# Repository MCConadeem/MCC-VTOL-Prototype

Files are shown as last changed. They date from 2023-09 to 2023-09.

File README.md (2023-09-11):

# MCC_VTOL_PROTOTYPE
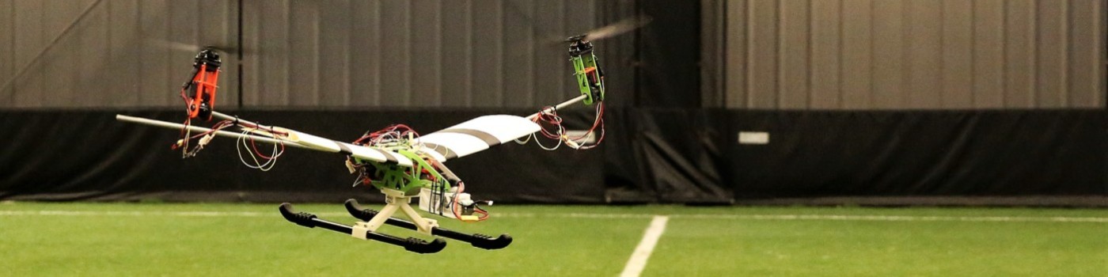
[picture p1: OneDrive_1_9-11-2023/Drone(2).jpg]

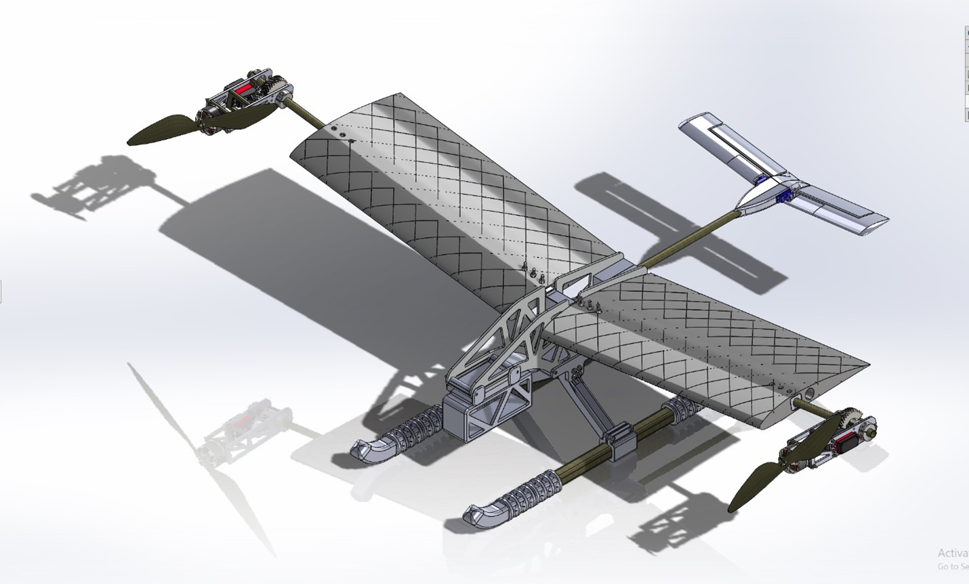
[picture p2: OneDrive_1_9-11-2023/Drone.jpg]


## Introductions

Hello, my name is Omar Nadeem and alongside Pioter Cetner and Maxim Karsav, we are currently undergoing the recreation of one of Tom Stanton's VTOL drones. This is our capstone project for our 2 years at Monroe Community College. For a full in-depth analysis, there will be an engineering notebook for our journey along the way as well as a final report documenting the over-all progress we achieved.

## File Structure
Folders are categorized in sub-assemblies then versions of the full assembly are used with the naming convention of vXXX with the X being replaced with a 0 or the next letter in the alphabet. 
The code for the following aircraft uses an Arduino based Flight Stabilization Package called dRehmflight created by Nicholas Rehm. This is under the dRehmFlight-Master folder. This is well documented and the modifications and our finished journals will be published here at the end of the project.

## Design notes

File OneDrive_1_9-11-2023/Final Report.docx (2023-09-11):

Monroe Community College

Elevation Nation

Maxim Karasev, Piotr Cetner, and Omar Nadeem

May 22nd, 2023

# 1. Executive Summary:

This executive summary provides an overview of our independent project focused on the development of a Vertical Take-Off and Landing (VTOL) Unmanned Aerial Vehicle (UAV). The project aimed to explore the advancements in VTOL technology at a hobbyist level and create a functioning prototype to be upscaled by future students.

Traditional aircraft designs, such as helicopters, planes, and multirotors, have inherent limitations in terms of maneuverability, adaptability, and efficiency. VTOL UAVs combine the vertical take-off and landing capabilities of helicopters and multirotors with the speed and efficiency of fixed-wing aircraft. We decided that a VTOL UAV was an optimal solution to overcome the limitations of traditional aircraft due to its unique combination of capabilities. By utilizing vertical take-off and landing, the VTOL can access confined or hard-to-reach areas, making it suitable for a wide range of applications where a plane simply could not. Furthermore, VTOL aircraft can take off from such an area and then transition to a forward flight mode, allowing it to regain all the traditional advantages a fixed-wing aircraft would have.

Throughout the project, we meticulously analyzed and iteratively improved the design of our VTOL. We encountered and successfully resolved several challenges, such as power distribution issues, control mixing and PID tuning, landing gear and battery mount optimization, and motor and ESC selection. These endeavors involved extensive troubleshooting, redesigning of components, and iterating 3D parts with new revisions. This meticulous approach to design analysis led to significant improvements. Notably, we fine-tuned the PID controls for each axis, ensuring stable and controlled vertical flight. The redesign of the landing gear and battery mount significantly improved rigidity, while the use of LW-HT-PLA material decreased the weight of the craft without sacrificing too much strength.

While we have achieved notable milestones in our project, such as winning the first-place prize in STEM at our college's scholar's day, there are still areas for further development. For example, we are exploring the integration of a DJI FPV camera using the QLiteOSD kit to enhance flight capabilities. The upcoming delivery of new motors will also enable us to continue our testing, expanding it into forward flight.

In conclusion, our independent project has proven to be a valuable exploration of VTOL technology. By combining vertical take-off and landing capabilities with adaptable flight modes, we have created a unique aircraft. By carefully analyzing our design, troubleshooting, and seeking continuous improvement, we have made considerable progress toward our objectives. Our ongoing dedication to the project's advancement ensures that we will continue refining and expanding the capabilities of our VTOL as time passes.

# 2. Table of Contents

Contents

# 3. Design Evolution

Our team embarked on an extensive design process to develop our VTOL. This section highlights the key stages and decisions we made throughout the design stage, providing insights into our design`\ process and the rationale behind our choices. We utilized a combination of CAD modeled parts, circuit schematics, and software code/flowcharts to outline our design journey.

- Initial Ideas and Conceptualization:

The design process began with brainstorming sessions where we explored various concepts and potential solutions. We were motivated by our fascination with VTOL technology and its advantages over traditional aircraft designs. After seeing a VTOL design by Tom Staton, an aerospace engineer, seamlessly transition between vertical take-off and landing and forward flight, we knew we had to build a VTOL ourselves. Initial sketches and concept diagrams captured our early ideas and formed the foundation of our design.

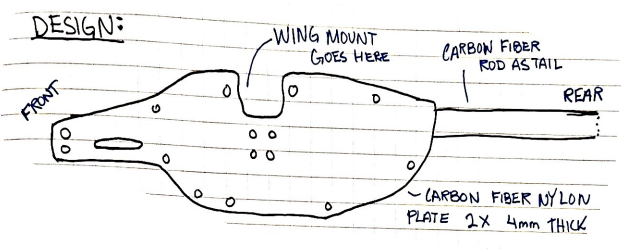
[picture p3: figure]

Figure 1: Initial Sketch

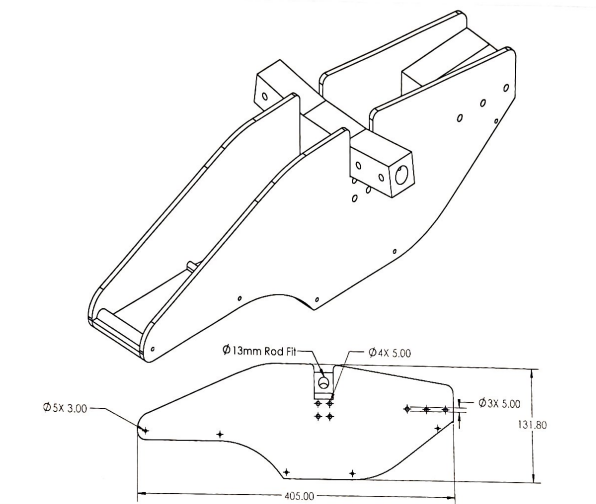
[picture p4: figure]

Figure 2: Initial Assembly

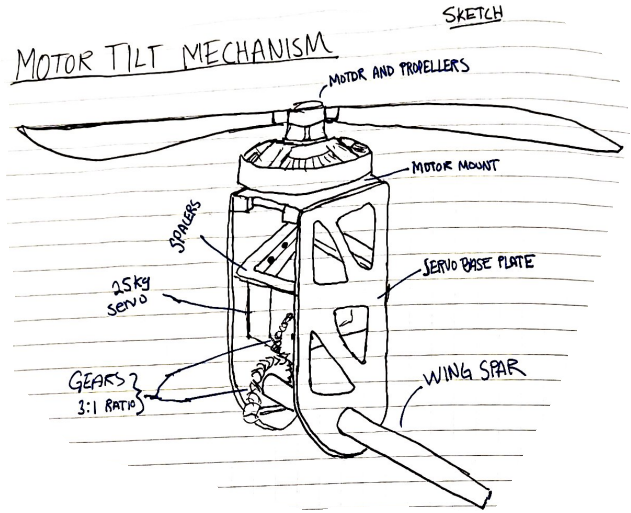
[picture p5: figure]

Figure 3: Motor Tilt Mechanism

- Additive Manufacturing for Rapid Prototyping and Iteration:

Recognizing the potential of 3D printing, we leveraged this technology to fabricate various components of our VTOL. Although we are all mechanical engineering students, and could have manufactured our parts via subtractive manufacturing, we intentionally chose not to do this. The ability to create complex geometries and intricate designs through 3D printing simplifies the design process immensely, as there is near no thought regarding how easy a part is to machine. Additionally, 3d printing reduces the amount of active labor required to prototype so many parts. Traditionally, creating a part for the first time requires someone to be actively working and monitoring any tooling, and this holds true for all future revisions of that part as well. Additive manufacturing allowed us to design a part, press print, go to class, and come back to the finished part in a few hours. If a part ever breaks or needs to be redesigned, then the same process holds true: press print, and come back a few hours later to a finished part. The time savings of additive manufacturing in prototyping is incredible; had we not had access to 3d printers, there is no way we would have been able to proceed at the rate we have been.

- System Architecture and Integration:

Once we had a rough idea of what we wanted to design, we focused on developing a robust system architecture. We identified the critical components, such as the flight controller, motor system, power distribution, and control system, and carefully planned their integration. SolidWorks images and circuit schematics were instrumental in visualizing and refining the system architecture, ensuring proper component placement and interconnectivity.

- Control Mixing and PID Tuning:

Achieving stable flight control was a crucial aspect of our design. We dedicated a considerable amount of time to control mixing and PID tuning, iteratively adjusting the control parameters to maximize performance. None of us had ever had to do any sort of PID tuning, so this was quite a learning experience for us. Software code and flowcharts were used to outline our control algorithms and visualize the flow of information between the inertial measurement unit (IMU) and the flight controller. This process allowed us to refine the control response and ensure stable flight characteristics.

Proportional Integral Derivative

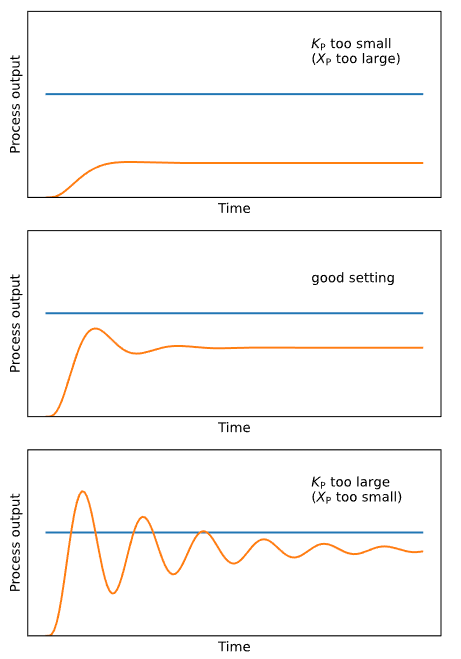
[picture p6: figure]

Figure 4: PID Graphs

1. Proportional Gain (KP): The proportional gain determines the strength of the corrective action applied by the controller. Increasing KP enhances system responsiveness but can introduce overshooting and oscillations, while decreasing KP reduces responsiveness and can result in sluggish behavior. The Proportional Range (XP) limits the range of error values where the proportional action is effective. A wider XP allows proportional control over a larger range, potentially leading to overshooting or instability, while a narrower XP reduces the influence of proportional control and responsiveness near the setpoint.
2. Integration Time (TI): The integration time determines the rate at which the integral action corrects for steady-state errors. Increasing TI strengthens the integral action and reduces steady-state errors, but excessively high values can introduce overshoot and instability.
3. Derivative Time (TD): The derivative time influences the controller's response to the rate of change of the error. Higher TD values introduce more damping, helping to prevent overshooting and oscillations, but extremely high values can introduce response delays and instability.
- Component Optimization and Redesign:

Throughout the design evolution, we encountered challenges and identified areas for improvement. The landing gear and battery mount, for instance, initially relied on zip ties, but we quickly realized the need for a more rigid and secure solution. We iterated on the design, utilizing ABS plastic parts clamped the components onto carbon fiber square rods with M5 bolts. This optimization significantly enhanced the structural integrity of the UAV. We documented these design iterations in our notebooks and captured revised sketches to track the progress.

Figure 5: Landing Gear Redesign

- Material Selection and Testing:

In pursuit of lightweight yet durable components, we explored various materials. Our experimentation led us to LW-HT-PLA, which exhibited superior flexibility and improved impact resistance compared to regular PLA. We tested the material by conducting destructive testing, observing how our wing segments broke when thrown at the ground. These observations allowed us to improve each successive revision of the wings and influenced the final material selection.

Figure 6: Broken Wing

- Future Enhancements:

While our design has reached an advanced stage, we continue to explore opportunities for further development. Integration of a DJI FPV camera using the QLiteOSD kit is one area we are actively working on. Additionally, the impending arrival of new motors will open avenues for testing and refining the forward flight capabilities of our VTOL. Our ongoing commitment to continuous improvement ensures that our design will evolve and adapt as we strive for enhanced performance and functionality.

The design evolution of our VTOL UAV highlights our iterative and detail-oriented approach. Through sketches, SolidWorks images, circuit schematics, and software code/flowcharts, we captured the progression of our design process. From conceptualization to component optimization and material selection, our team's dedication to refinement has shaped the final solution and laid the groundwork for future advancements in VTOL technology.

# 4. UAV Operation

The operational aspects can be attributed to effective PID tuning where it played a crucial role in achieving stable flight by regulating the motor speeds and control surfaces to maintain a balanced and controlled hover. The PID controller monitored the drone's orientation and altitude, adjusting the motor speeds and control surfaces to maintain a stable hover. Through careful tuning of the PID parameters, we were able to achieve a well-balanced hover, where the drone maintained its position and altitude without drifting or exhibiting erratic behavior. After multiple hover tests, we fine-tuned our PID values to create a more stable flight.

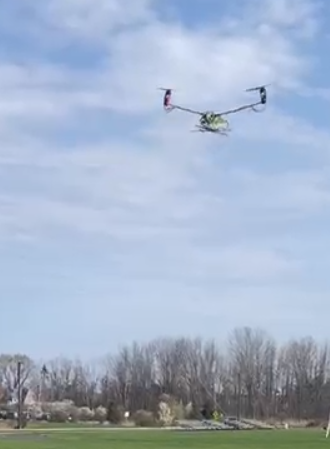
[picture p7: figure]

Figure 7: First Flight

The VTOL prototype demonstrated the ability to hover with only two motors, and this is possible due to the principle of rotational equilibrium and torque balance. When the two motors spin in opposite directions, they create equal and opposite torques, which cancel each other out. This equilibrium allows the drone to hover vertically without any roll or yaw motion.

By carefully adjusting the motor speeds and control surfaces using the PID controller, we were able to maintain this torque balance and achieve a stable hover. The two motors provided the necessary lift to counteract the force of gravity, while the control surfaces helped in adjusting the drone's orientation and stability. It is important to note that achieving a stable hover with only two motors requires precise control and balancing of forces. Any deviation in the motor speeds or control surface inputs can disrupt the torque balance and result in instability or undesired motion. Therefore, the accurate PID tuning and understanding of the physics of vertical flight were essential factors in the success of our hover test.

Overall, the combination of effective PID tuning and a thorough understanding of the physics involved in vertical flight enabled our VTOL prototype to hover successfully, demonstrating its operational capabilities and paving the way for further development and exploration of its flight capabilities.

# 5. Electronics and Software

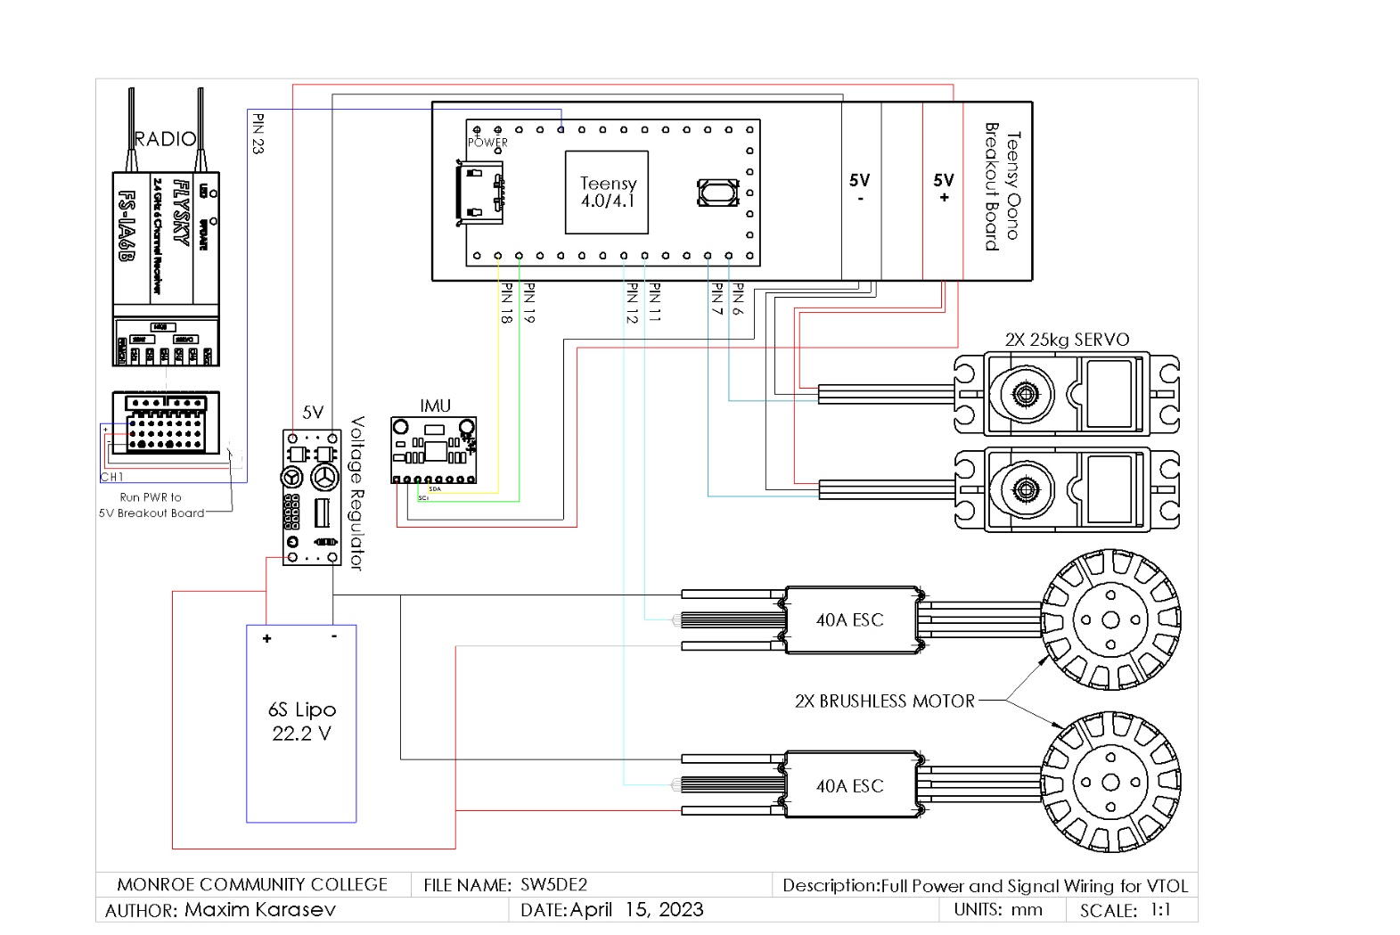
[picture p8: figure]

Figure 8: Circuit Diagram

The electronic circuitry of the project consists of a Teensy 4.0/4.1 microcontroller running the dRehmflight Arduino software developed by Nicholas Rehm. The Teensy serves as the flight controller unit for the project, handling various inputs and outputs.

The Teensy receives signals from two sources: an FS-I6B receiver and an MPU6050 IMU (Inertial Measurement Unit). The FS-I6B receiver is responsible for receiving remote control signals, allowing the user to control the drone. Since we are using PPM (Pulse Position Modulation) as our RX output we only need 1 wire for all 6 channels instead of an individual wire for each channel with SBUS (Serial BUS). The IMU captures motion data from various sensors such as accelerometers, gyroscopes, and magnetometers, providing information about the aircraft's orientation and movement.

The Teensy then processes these input signals and sends commands to several components. The electronic speed controllers (ESCs) receive signals from the Teensy, controlling the motors' speed and direction. This allows the aircraft to achieve controlled movement and adjust its thrust. Additionally, the Teensy sends signals to servos, which are responsible for tilting the motors. By adjusting the servos' positions, the aircraft's pitch and roll can be controlled, enhancing stability and maneuverability.

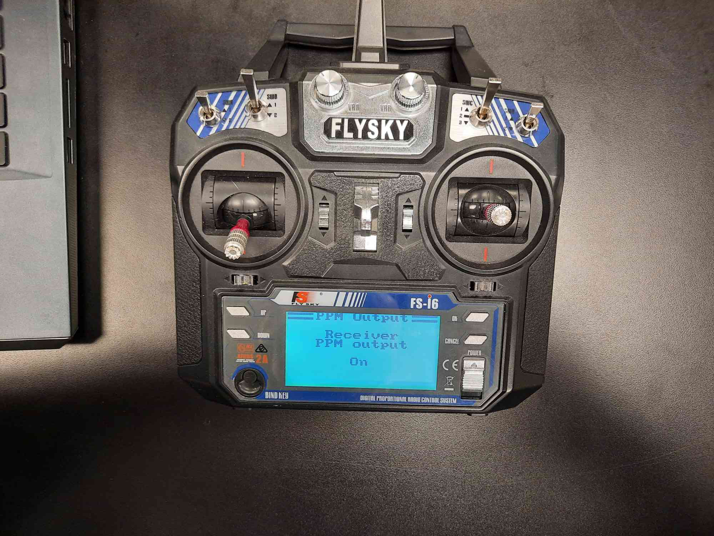
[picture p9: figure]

Figure 9: PPM Output

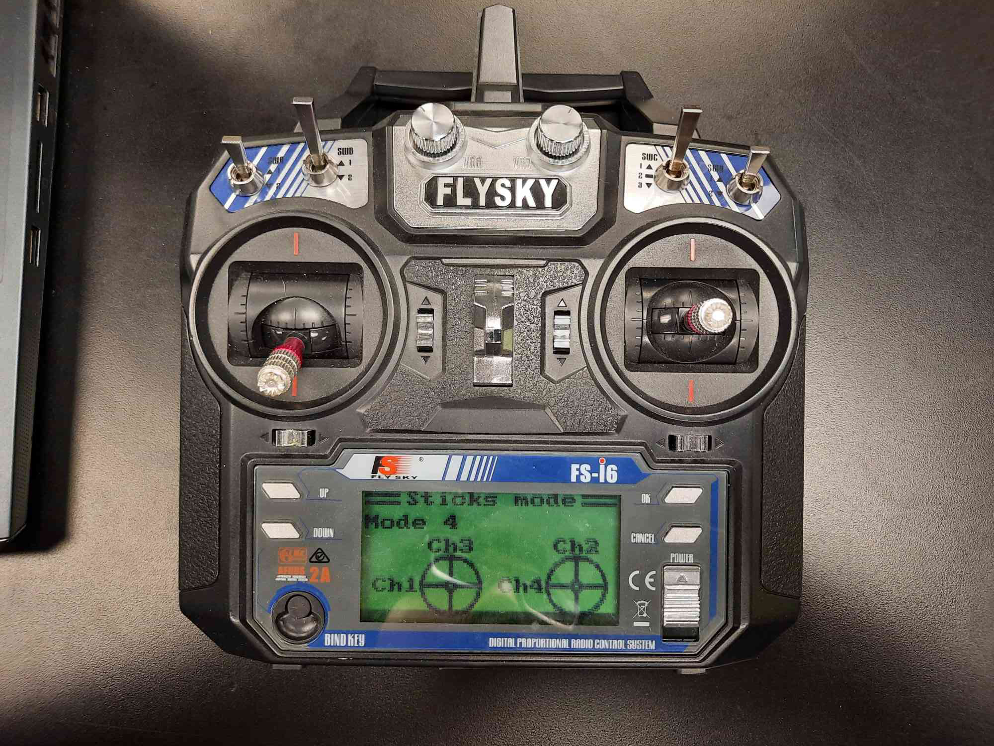
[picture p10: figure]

Figure 10: Sticks Mode

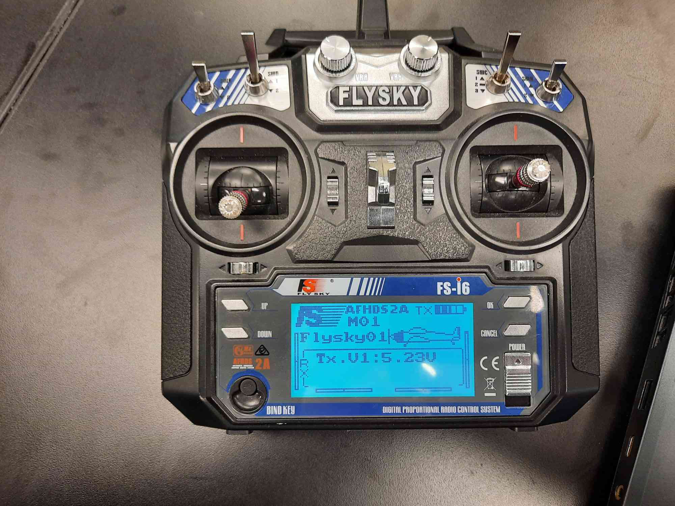
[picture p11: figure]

Figure 11: Trim (Red boxes are where the trim is visually indicated)

The transmitter has multiple settings that are important to note. To simplify the wiring on the drone, we are using PPM on the receiver, so we must make sure the transmitter is outputting the same way. So, on the transmitter PPM output must be activated as seen in figure 9. The next thing is the channels must correspond to what the channels are in the code, so under sticks mode we can change which channels are assigned to which stick. See figure 10. Channels 5 & 6 are auxiliary switches for mode switch and arm. Lastly while flying the drone, you can perform trim which tunes each channel. zero position. This allows you to re-zero the craft’s throttle, roll, pitch, and yaw axis of rotations. These are indicated in the transmitter’s main display as the vertical/horizontal bars which a slider in them. See figure 11.

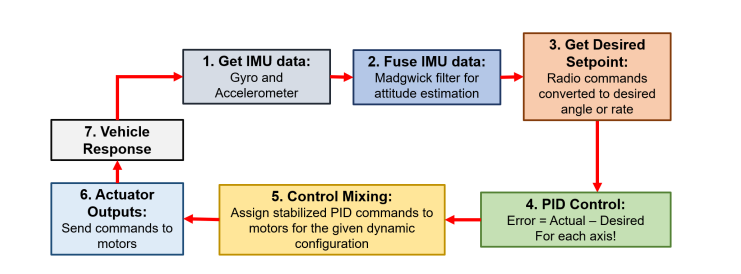
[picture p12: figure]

Figure 12: dRehmFlight control loop (Credit to Nicholas Rehm)

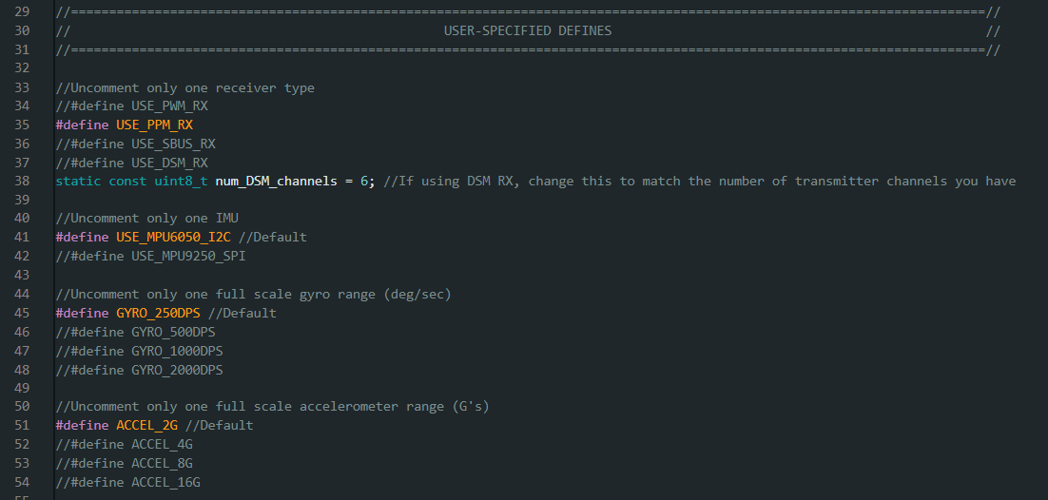
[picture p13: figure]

Figure 13: Hardware Declaration

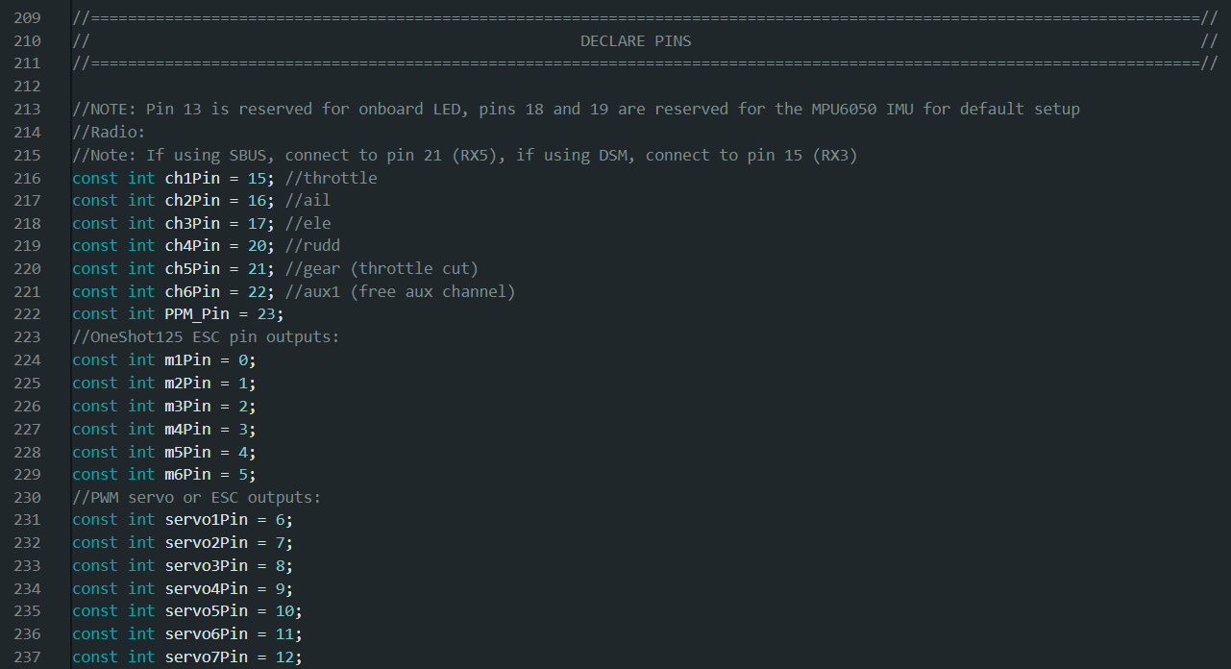
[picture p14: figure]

Figure 14: Pin Declarations

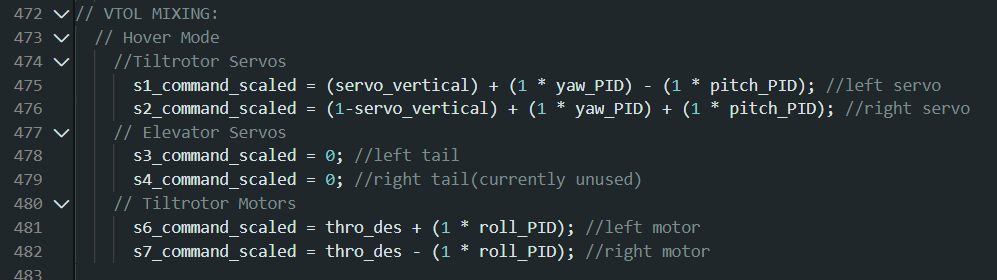
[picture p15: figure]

\

Figure 15: Control Mixing

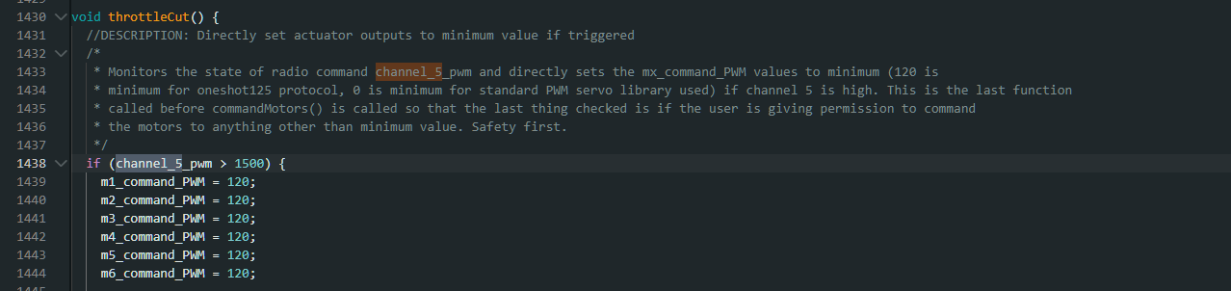
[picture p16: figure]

Figure 16: Throttle Cut Channel Assignment

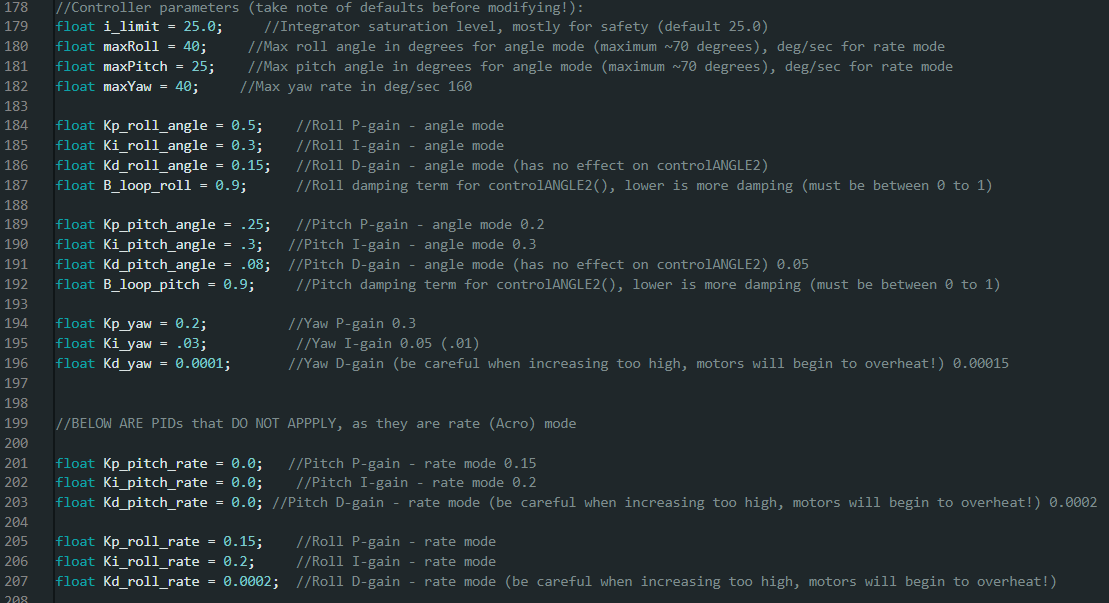
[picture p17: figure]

Figure 17: PID Tuning

The language we are using to code Teensy is Arduino. This language is versatile and has many packages available for almost any use case. A plug-in, Teensyduino created by Paul Stoffregen is used for USB serial connection to the Teensy.

The dRehmflight stabilization package created by Nicholas Rehm provides the framework for creating your own control mixing and tuning for manual flight and auto stabilization. The sections of the code that we edited were the radio, pin declarations, the control mixer function, and the PID values. These were changed in accordance with our specifications for the bi-copter tiltrotor design. The PID values were changed through experimentation. The experimentation involved having the craft held preventing takeoff however had enough degree of freedom to notice if it was drifting in the wrong direction. We did differential thrust (roll) first then yaw and finally pitch tuning in the gym and PAC center here on campus. Currently there is only a hover mode in the code. In the future we will be using Channel 6 switch to have a transition mode that flips between hover and forward flight. Channel 5 is a 2-mode switch which arms the motors giving us the most basic type of failsafe, a kill switch.

# 6. Fabrication Methods

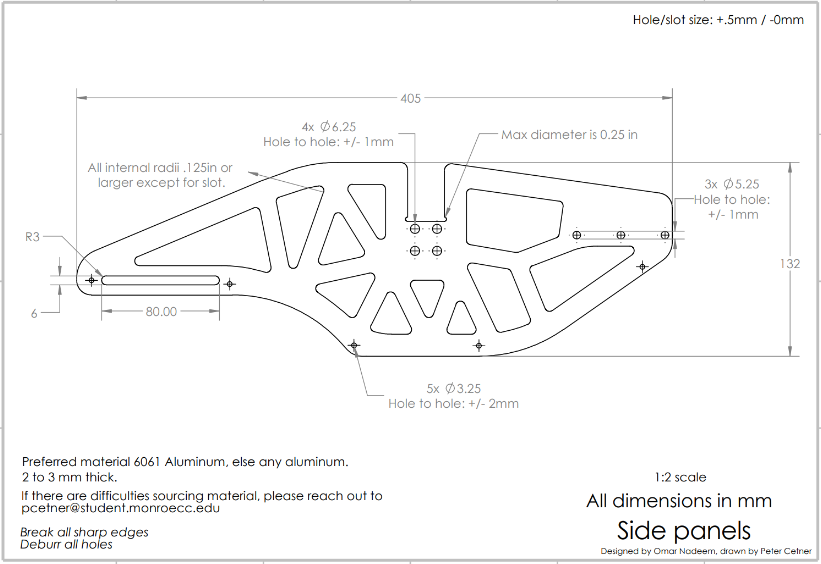
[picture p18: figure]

Figure 18: Side Panel Drawings

Side panels which we 3D printed in PLA because we were not able to get our own machinists to make one in time.

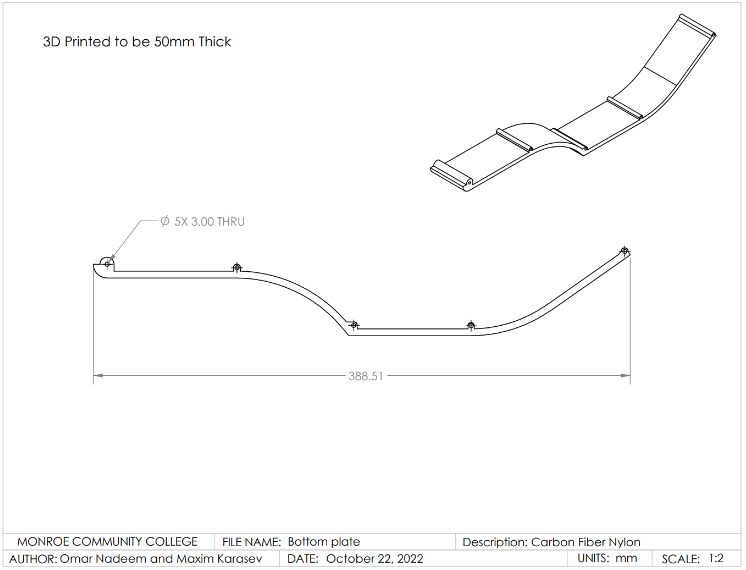
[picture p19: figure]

Figure 19: Bottom plate that attaches side panels.

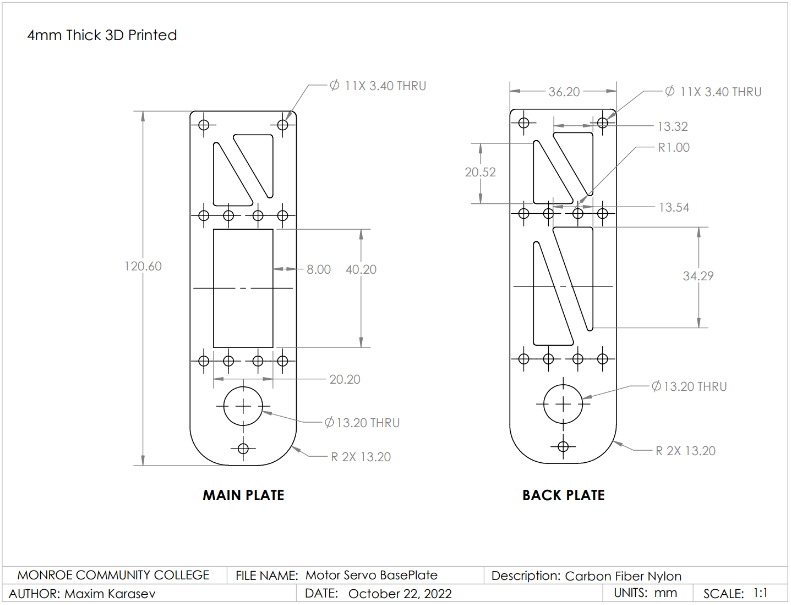
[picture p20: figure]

Figure 20: Base plates for the tilt-mechanism that was originally going to be machined but opted to 3D print in PLA for the prototype.

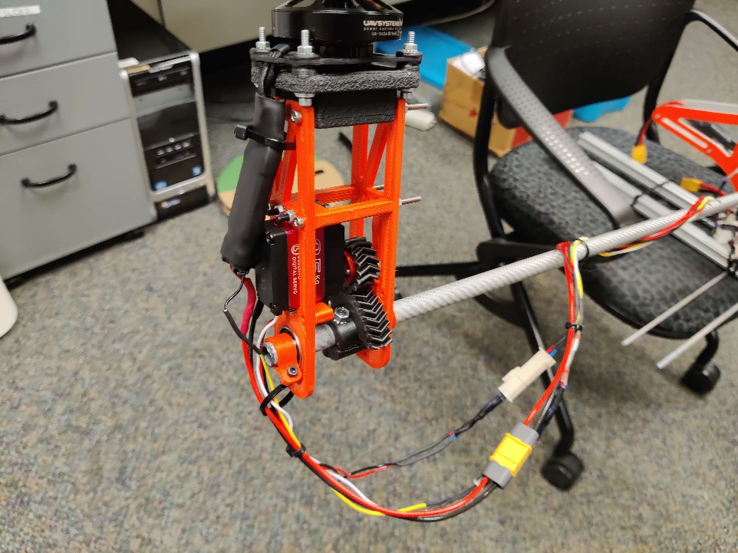
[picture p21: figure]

Figure 21: 3D Tilt-Mechanism Assembly

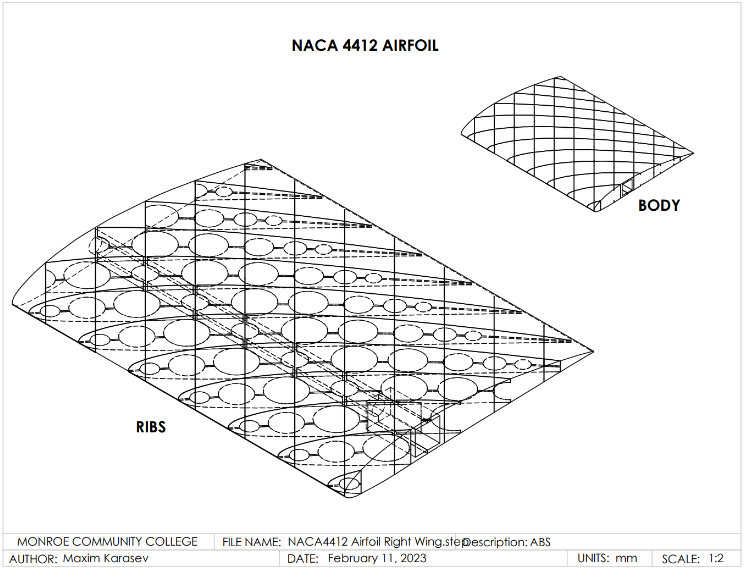
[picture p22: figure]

Figure 22: NACA 4412 Airfoil that was 3D printed in heat resistant light-weight PLA in the final.

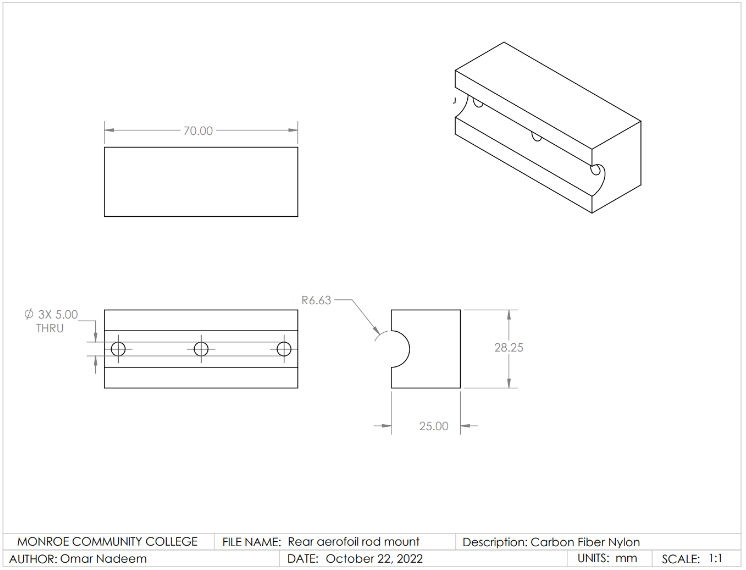
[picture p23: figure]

Figure 23: This attaches to the rear of the side panels to hold the rear carbon fiber rod as tail.

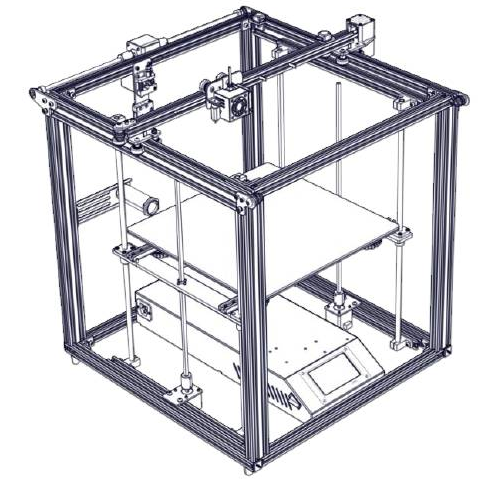
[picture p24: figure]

Ender 5 Plus 3D Printer Method X 3D Printer

Figure 24: 3d Printers

We used the Ender 5 Plus to 3D print parts in PLA or lightweight PLA. Most of our designed parts were fabricated through PLA. We used the Method X for any part that needs to be printed in a stronger material which was Carbon Fiber Nylon. This allowed for any parts that have a lot of forces at play to be stable and reduce the chances of failure.

# 7. Design Analysis:

The design for the tiltrotors provides a reliable and stable way of controlling the thrust vectors of our motors. This allows us to perform stable flight and maintain hover through the stabilization code. Our first test flight was successful in getting off the ground but some more tuning was required as it was unstable in some axis’s. Due to the wind, we couldn’t properly adjust our transmitter trim so after the first flight we headed inside to the PAC center, an indoor field, to tune it further. This proved very useful as it allowed us to further finetune the PID values. This led to the drone being able to take off and the stabilization code kept it in place hovering.

From this stage we redesigned our landing gears as seen in figure 5, moved the battery to the nose and added wings to our carbon fiber rods. This was all done in preparation for the forward flight transition test. With all these redesigns we will need to redo our PID & trim tuning for the hover mode. The forward flight capabilities of this drone are still in progress as we design and prototype the tail section for pitch control in the forward flight. We will also have to add in the forward flight and 2-mode transition switch.

https://youtu.be/snkThKrBGW0

Figure 25: First Flight Video

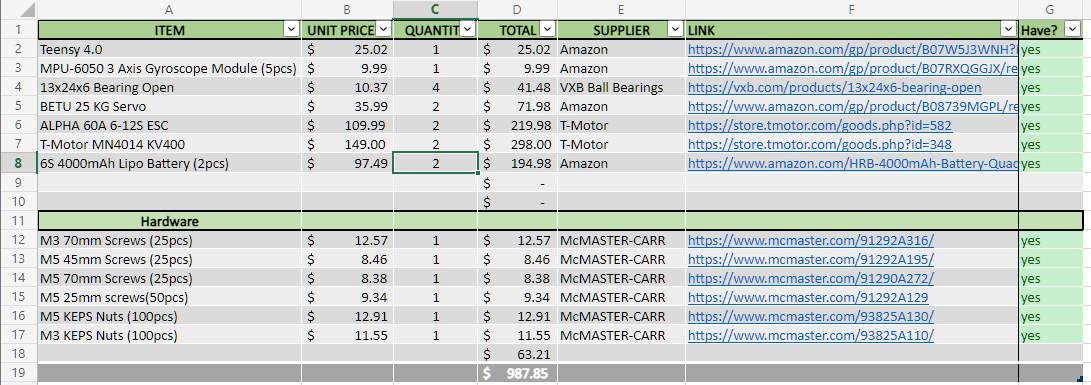
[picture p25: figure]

Figure 26: Bill of Materials

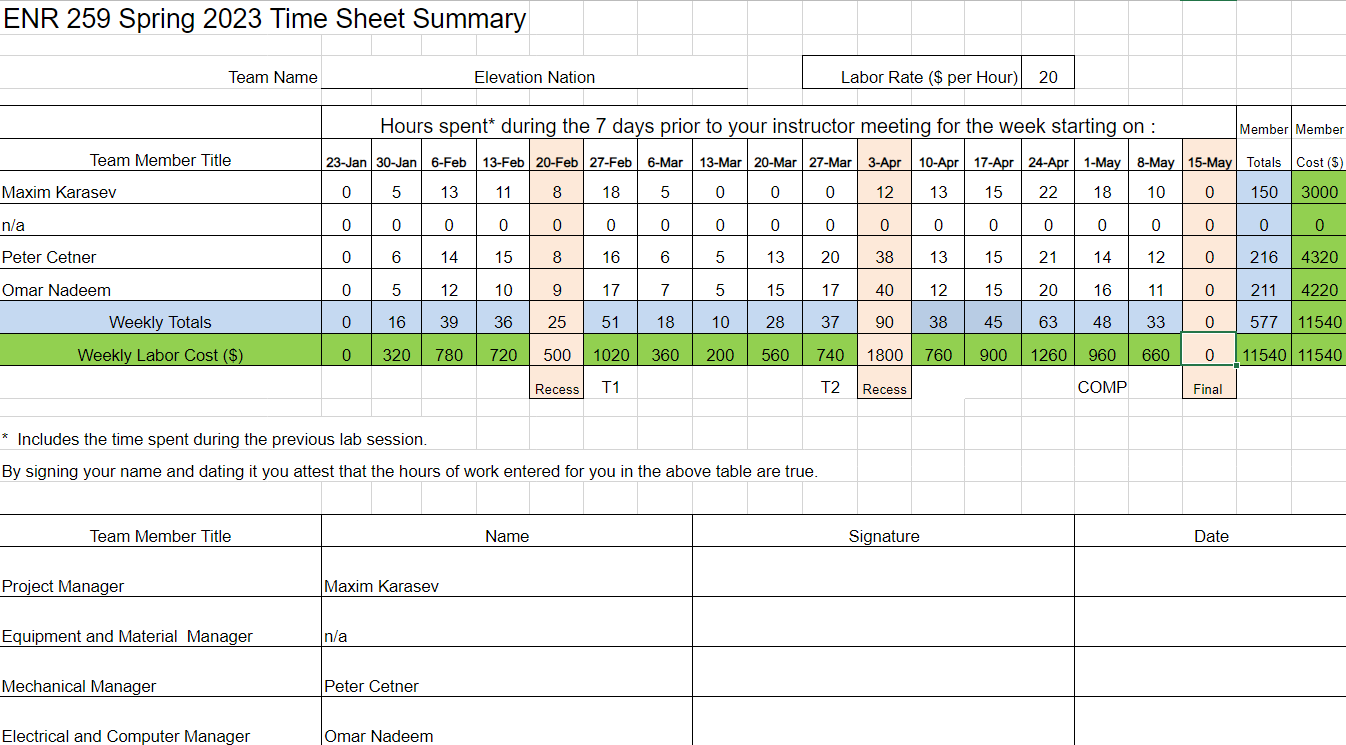
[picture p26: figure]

Figure 27: Time Sheet

# 8. Team and Technical Analysis

a. Team Functionality:

Throughout this project, our team functioned cohesively and effectively. We communicated clearly through a hybrid approach, using discord as well as in-person meetings. We assigned specific roles and responsibilities to each team member and maintained regular meetings to track progress and discuss challenges as they occurred. Collaboration and teamwork were strong, with each member actively contributing their skills to the project. Our work environment encouraged open discussions and idea sharing, which helped us have good brainstorming sessions and come up with good solutions to problems.

b. Problem Identification and Resolution:

While our team functioned well overall, no engineering project would be complete without a few hiccups along the way. One notable issue was the power distribution problem we ran into, where the current drawn from the motors caused a voltage drop at the teensy. To address this, we conducted thorough research, consulted technical resources, and experimented with different battery configurations until we found the problem, and then implemented an effective solution. Additionally, we faced difficulties with control mixing and PID tuning, leading to unstable flight characteristics. To rectify this, we dedicated time to studying PID control theory, fine-tuned the PID parameters, and conducted numerous flight tests to achieve stable flight performance.

c. Potential Team Structure Improvements:

If we were to repeat this project, we would consider adjusting the team structure to ensure a more even distribution of workload and specialization. While our current structure worked well, we believe a more rigidly defined division of tasks and responsibilities, tailored to each of our strengths and interests, would further optimize our productivity. Additionally, we feel that having more team members with varied disciplines would have been helpful. Having only three mechanical engineers made it very difficult to do any electrical and software work, as it was very slow and tedious.

d. Appropriateness of Components and Methods:

Our team carefully evaluated and selected components and methods that aligned with the requirements and objectives of the project. The decision to use additive manufacturing, specifically 3D printing, proved to be extraordinarily effective for rapid prototyping and iteration. We utilized off-the-shelf electronics, such as motors and ESCs, that were suitable for our project requirements and integrated well with our custom-designed components.

e. Effective Design Decisions and Challenges:

Several design decisions proved successful in achieving our goals. The redesign of the landing gear and battery mount using ABS 3D-printed parts significantly improved rigidity and durability, addressing the previous revision which used zip ties. The utilization of LW-HT-PLA material for the wing sections enhanced impact resistance without compromising weight. These design decisions contributed to the overall functionality and performance of the UAV. However, we encountered challenges with one of, leading to the decision to replace the motors and ESCs. While this incurred additional costs, it was a necessary step to ensure safety and reliability during the flight. Our initial intention was to use spare motors and ESCs to save costs, but in hindsight, we should have considered alternative motor options earlier in the design process.

f. Potential Design Choice Modifications:

If we were to repeat the project, which the MCC drone team essentially will be doing next year, we would refine our design choices based on the lessons learned during this iteration. Specifically, we start the design process by selecting motors, ESCs, and a power system, then designing an aircraft around that. Additionally, we would explore advanced motor control techniques to further optimize motor performance and efficiency. Furthermore, we would invest more time in aerodynamic analysis and optimization to improve the overall flight characteristics and efficiency of our UAV. By keeping in mind these potential changes, we believe our future design choices would result in an even more refined and efficient VTOL UAV, enhancing its capabilities and expanding its potential applications.

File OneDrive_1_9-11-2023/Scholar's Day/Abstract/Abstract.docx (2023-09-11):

From Concept to Prototype: The Development of a Tilt-Rotor VTOL Drone

Vertical take-off and landing (VTOL) aircraft have seen an increase in usage and development because of their unique flight characteristics. Our goal with our tilt-rotor VTOL drone is to combine the benefits of a quadcopter and a fixed-wing aircraft for future Student Unmanned Aerial Systems (SUAS) competitions. Some of the advantages of a VTOL platform include not needing a runway to take off, gaining a stable stationary platform to use other mechanisms while in mid-flight, and increasing our flight range and cruise speed by transitioning to forward flight.

We began our project researching types of VTOL aircraft looking for a simple yet effective solution that included the following factors: weight, robustness, and reliability. Finally, we decided on the tilt-rotor design because it best met our criteria while also resembling the V22 Osprey currently in service with the US military. We then used CAD software to design and prototype our aircraft. By using traditional subtractive and newer additive manufacturing, we were able to quickly manufacture and assemble the prototype. We are now in the testing phase of the project, which will include verifying the drone's hovering and transitioning capabilities, followed by a full-flight demonstration. We are excited to see the valuable insights that will improve future project iterations.

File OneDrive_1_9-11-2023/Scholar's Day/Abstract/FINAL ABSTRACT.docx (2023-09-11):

From Concept to Prototype: The Development of a Tilt-Rotor VTOL Drone

Vertical take-off and landing (VTOL) aircraft have seen an increase in usage and development because of their unique flight characteristics. The goal of this project is to combine the benefits of a quadcopter and a fixed-wing aircraft by designing a tilt-rotor VTOL drone, allowing us to use it as a testing platform as we design and build an upscaled version of the project. Some of the advantages of a VTOL platform include not needing a runway to take off, gaining a stable stationary platform to use other mechanisms while in mid-flight, and increasing our flight range and cruise speed by transitioning to forward flight.

We began our project researching types of VTOL aircraft looking for a simple yet effective solution that included the following factors: weight, robustness, and reliability. We then used computer-aided design (CAD) software to design and prototype our aircraft. By using traditional subtractive and newer additive manufacturing technologies, we were able to quickly manufacture and assemble the prototype. We revised the parts as needed after identifying design flaws that occurred in the design phase or manufacturing. This presentation will review the testing phase of the project, which will include verifying the drone's hovering and transitioning capabilities, as well as a full-flight demonstration. The testing phase provides valuable insights that will improve future project iterations.

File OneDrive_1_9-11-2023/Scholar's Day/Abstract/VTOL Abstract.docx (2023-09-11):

Peter’s:

Vertical take-off and landing (VTOL) vehicles have gained significant attention in recent years due to their potential to revolutionize transportation. Our research focuses on prototyping a VTOL in order to gain a stronger understanding of how they function. To begin our project, we conducted extensive research into the design and operational principles of VTOL aircraft. We then used that knowledge to create a detailed design of our VTOL, taking into account factors such as weight, robustness, and reliability. Once the design phase was completed, we began the construction phase of the project. By using a combination of traditional subtractive manufacturing as well as newer additive manufacturing, we were able to quickly manufacture and assemble our prototype. At this point, we are eagerly looking forward to conducting a thorough evaluation of the craft's capabilities in the upcoming testing phase. We hope that this prototype will provide us with valuable insights that will improve our future iterations of the project.

Omar’s:

Abstract

Vertical take-off and landing (VTOL) aircraft have seen a rise in usage and development for the commercial industry. These VTOL aircraft are quite versatile in their functionality and how far of a distance they can travel. Our goal with our tiltrotor VTOL drone is to create a mix between a quadcopter and a fixed-wing aircraft to gain the benefits of both for future Student Unmanned Aerial Systems (SUAS) competitions. The benefits of the VTOL capabilities are that we would require no runway to take off and gain a stable stationary platform to use other mechanisms mid-flight. The fixed-wing benefits are that we increase our flight range and cruise speed by transitioning to having the wings create our lift instead of motors.

We began our project researching types of VTOL aircraft looking for a simple yet effective solution that included the following factors: weight, robustness, and reliability. Finally, we decided on the tilt-rotor design because it best met our criteria while also resembling the V22 Osprey currently in service with the US military. We then used CAD software to design and prototype our aircraft. By using traditional subtractive and newer additive manufacturing, we were able to quickly and repeatably manufacture and assemble the prototype. Currently, we are approaching the first testing of the hover and are excited to see the valuable insights that those results will give us for future iterations of the project.

Merged:

From Concept to Prototype: The Development of a Tilt-Rotor VTOL Drone

Because of their unique flight characteristics, vertical take-off and landing (VTOL) aircraft have seen an increase in usage and development. Our goal with our tilt-rotor VTOL drone is to combine the benefits of a quadcopter and a fixed-wing aircraft for future Student Unmanned Aerial Systems (SUAS) competitions. Some of the advantages of a VTOL platform include not needing a runway to take off, gaining a stable stationary platform to use other mechanisms while in mid-flight, and increasing our flight range and cruise speed by transitioning to forward flight.

We began our project researching types of VTOL aircraft looking for a simple yet effective solution that included the following factors: weight, robustness, and reliability. Finally, we decided on the tilt-rotor design because it best met our criteria while also resembling the V22 Osprey currently in service with the US military. We then used CAD software to design and prototype our aircraft. By using traditional subtractive and newer additive manufacturing, we were able to quickly manufacture and assemble the prototype. We are now in the testing phase of the project, which will include verifying the drone's hovering and transitioning capabilities, followed by a full-flight demonstration. We are excited to see the valuable insights that will improve future project iterations.

Ben Revision

From Concept to Prototype: The Development of a Tilt-Rotor VTOL Drone

Vertical take-off and landing (VTOL) aircraft have seen an increase in usage and development because of their unique flight characteristics. The goal of this project is to combine the benefits of a quadcopter and a fixed-wing aircraft by designing a tilt-rotor VTOL drone, allowing us to use it as a testing platform as we design and build an upscaled version of the project. Some of the advantages of a VTOL platform include not needing a runway to take off, gaining a stable stationary platform to use other mechanisms while in mid-flight, and increasing our flight range and cruise speed by transitioning to forward flight.

We began our project researching types of VTOL aircraft looking for a simple yet effective solution that included the following factors: weight, robustness, and reliability. We then used computer-aided design (CAD) software to design and prototype our aircraft. By using traditional subtractive and newer additive manufacturing, we were able to quickly manufacture and assemble the prototype. We revised the parts as needed after identifying design flaws that occurred in the design phase or manufacturing. This presentation will review the testing phase of the project, which will include verifying the drone's hovering and transitioning capabilities, as well as a full-flight demonstration. The testing phase provides valuable insights that will improve future project iterations.

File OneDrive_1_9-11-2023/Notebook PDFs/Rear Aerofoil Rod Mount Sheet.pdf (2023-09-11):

AUTHOR: Omar Nadeem; DATE: October 22, 2022; UNITS: mm; SCALE: 1:1; 3X 5.00 THRU

MONROE COMMUNITY COLLEGE | FILE NAME: Rear aerofoil rod mount | Description: Carbon Fiber Nylon

SOLIDWORKS Educational Product. For Instructional Use Only.

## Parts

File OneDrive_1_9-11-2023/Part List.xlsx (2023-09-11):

ITEM | UNIT PRICE | QUANTITY | TOTAL | SUPPLIER | LINK | Have?
Teensy 4.0 | $25.02 | 1 | $25.02 | Amazon | https://www.amazon.com/gp/product/B07W5J3WNH?linkId=51ce28bc664cb3264a8965efefd69c26&language=en_US | yes
MPU-6050 3 Axis Gyroscope Module (5pcs) | $9.99 | 1 | $9.99 | Amazon | https://www.amazon.com/gp/product/B07RXQGGJX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 | yes
13x24x6 Bearing Open | $10.37 | 4 | $41.48 | VXB Ball Bearings | https://vxb.com/products/13x24x6-bearing-open | yes
BETU 25 KG Servo | $35.99 | 2 | $71.98 | Amazon | https://www.amazon.com/gp/product/B08739MGPL/ref=ewc_pr_img_5?smid=A34YU2DWGOTPQX&psc=1 | yes
ALPHA 60A 6-12S ESC | $109.99 | 2 | $219.98 | T-Motor | https://store.tmotor.com/goods.php?id=582 | yes
T-Motor MN4014 KV400 | $149.00 | 2 | $298.00 | T-Motor | https://store.tmotor.com/goods.php?id=348 | yes
6S 4000mAh Lipo Battery (2pcs) | $97.49 | 2 | $194.98 | Amazon | https://www.amazon.com/HRB-4000mAh-Battery-Quadcopter-Helicopter/dp/B07VM4S36R | yes
 |  |  | $0.00
 |  |  | $0.00
Hardware
M3 70mm Screws (25pcs) | $12.57 | 1 | $12.57 | McMASTER-CARR | https://www.mcmaster.com/91292A316/ | yes
M5 45mm Screws (25pcs) | $8.46 | 1 | $8.46 | McMASTER-CARR | https://www.mcmaster.com/91292A195/ | yes
M5 70mm Screws (25pcs) | $8.38 | 1 | $8.38 | McMASTER-CARR | https://www.mcmaster.com/91290A272/ | yes
M5 25mm screws(50pcs) | $9.34 | 1 | $9.34 | McMASTER-CARR | https://www.mcmaster.com/91292A129 | yes
M5 KEPS Nuts (100pcs) | $12.91 | 1 | $12.91 | McMASTER-CARR | https://www.mcmaster.com/93825A130/ | yes
M3 KEPS Nuts (100pcs) | $11.55 | 1 | $11.55 | McMASTER-CARR | https://www.mcmaster.com/93825A110/ | yes
 |  |  | $63.21
 |  |  | $987.85

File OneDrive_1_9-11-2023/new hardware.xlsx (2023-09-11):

Link | Part | Buy QTY
https://vxb.com/products/13x24x6-bearing-open | Metal bearing for tilt mechanism, need 2 for each side | 4PCS
https://www.amazon.com/gp/product/B08739MGPL/ref=ewc_pr_img_5?smid=A34YU2DWGOTPQX&psc=1 | large degree of motion servo, need one for each side | 1PCS
1.000000 0.001300
0.950000 0.014700
0.900000 0.027100
0.800000 0.048900
0.700000 0.066900
0.600000 0.081400
0.500000 0.091900
0.400000 0.098000
0.300000 0.097600
0.250000 0.094100
0.200000 0.088000
0.150000 0.078900
0.100000 0.065900
0.075000 0.057600
0.050000 0.047300
0.025000 0.033900
0.012500 0.024400
0.000000 0.000000
0.012500 -0.014300
0.025000 -0.019500
0.050000 -0.024900
0.075000 -0.027400
0.100000 -0.028600
0.150000 -0.028800
0.200000 -0.027400
0.250000 -0.025000
0.300000 -0.022600
0.400000 -0.018000
0.500000 -0.014000
0.600000 -0.010000
0.700000 -0.006500
0.800000 -0.003900
0.900000 -0.002200
0.950000 -0.001600
1.000000 -0.001300

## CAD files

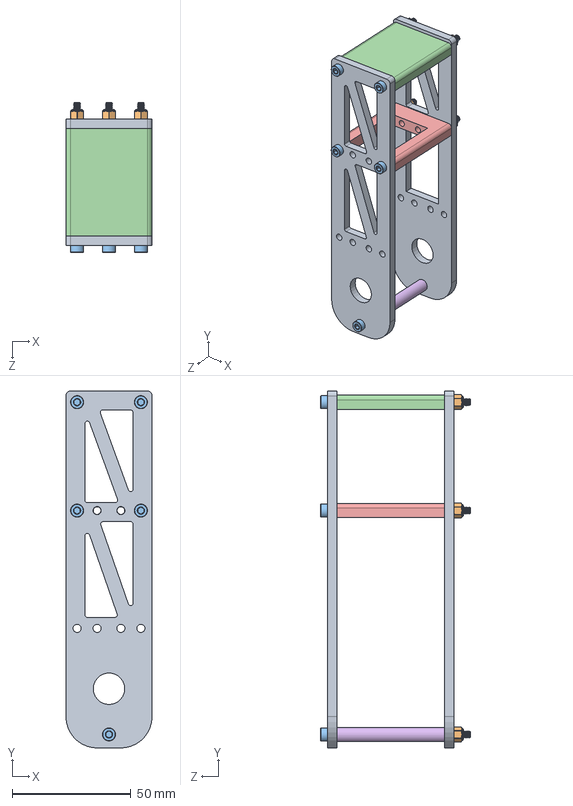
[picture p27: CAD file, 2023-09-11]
OneDrive_1_9-11-2023/Motor Servo/Wingtip servo motor mount.SLDASM
36.2 x 150.0 x 63.0 mm
Motor Servo BasePlate v1 x 2
93625A100_18-8 Stainless Steel Nylon-Insert Locknut x 5
91290A181_Alloy Steel Socket Head Screw x 5
Motor Servo top spacer
Motor Servo middle spacer
Motor Servo Bottom Spacer

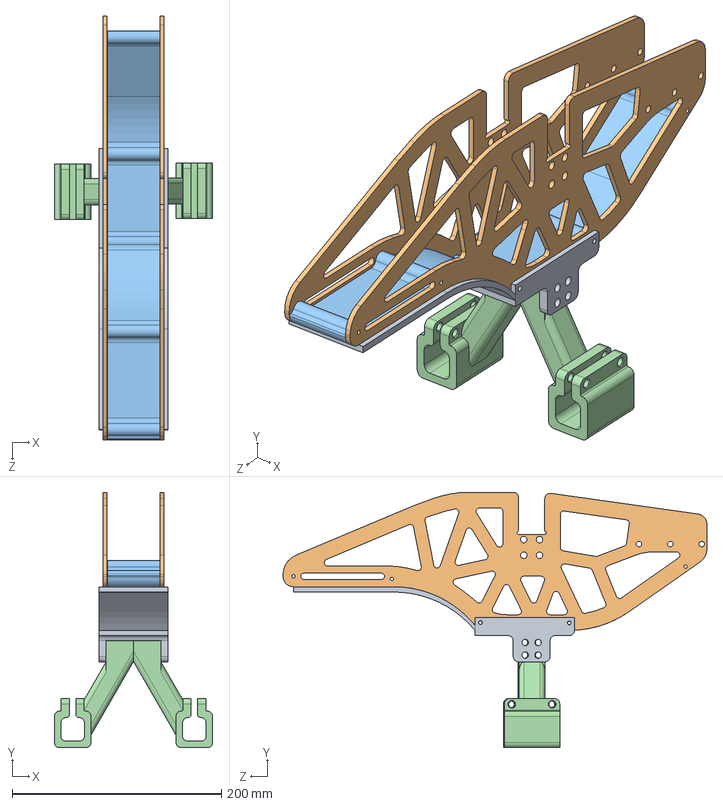
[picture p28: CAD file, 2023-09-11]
OneDrive_1_9-11-2023/Mounts/Landing Gear/Gear Assembly.SLDASM
151.2 x 244.0 x 405.0 mm
Bottom Mount
Side panels v1 x 2
BOTTOMPLATE_REV00B
Clamp x 2

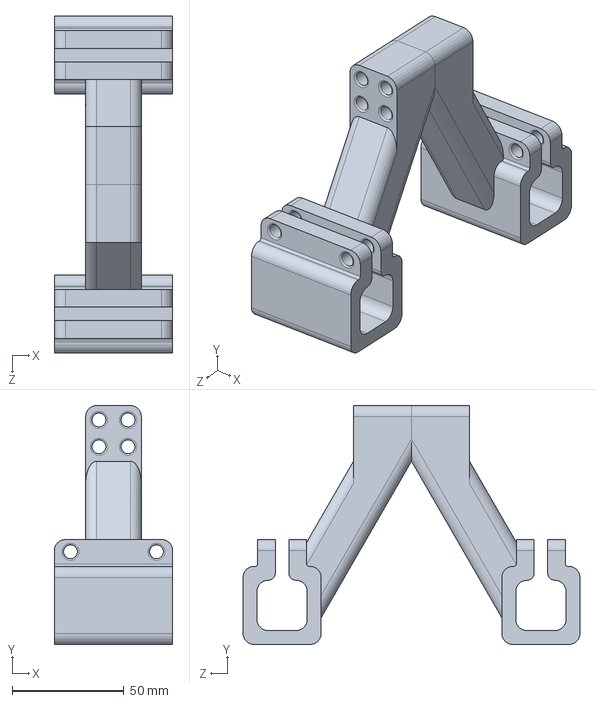
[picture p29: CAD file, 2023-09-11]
OneDrive_1_9-11-2023/Mounts/Landing Gear/Landing Gear Assembly.SLDASM
53.0 x 107.0 x 150.8 mm
Clamp x 2

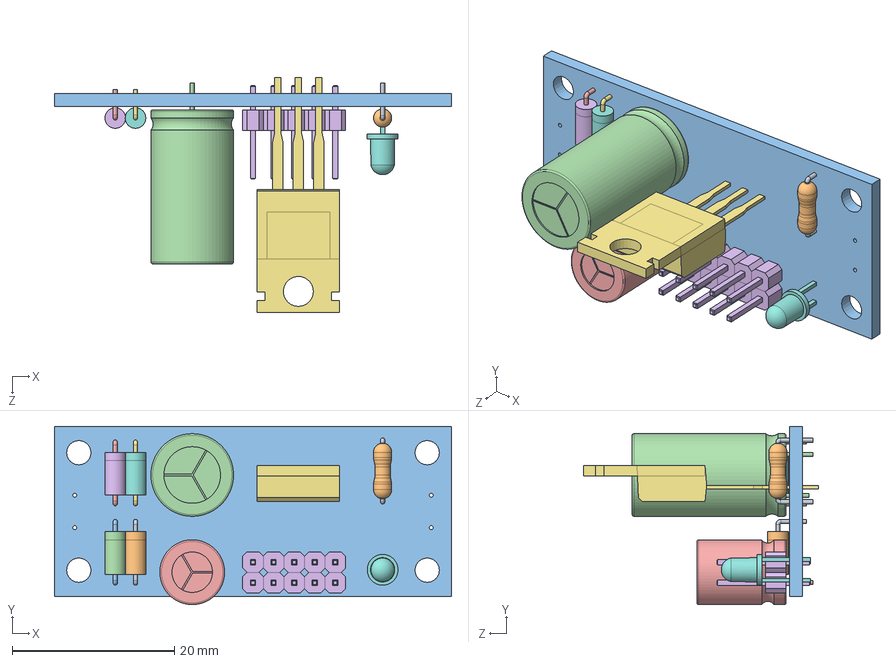
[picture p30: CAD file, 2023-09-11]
OneDrive_1_9-11-2023/Wiring Diagram/00A/regulator board 78XX.SLDASM
49.0 x 22.0 x 29.0 mm
Sweep.step
Pad001.step
Sweep001.step
Pad002.step
Sweep002.step
Pad003.step
Sweep003.step
Pad004.step
resistor 1_4W001.step
res.step
PCB.step
cap 470-35V.step
cap 100-35V.step
Header 10 pins.step
regulator 78XX.step
led 3mm.step

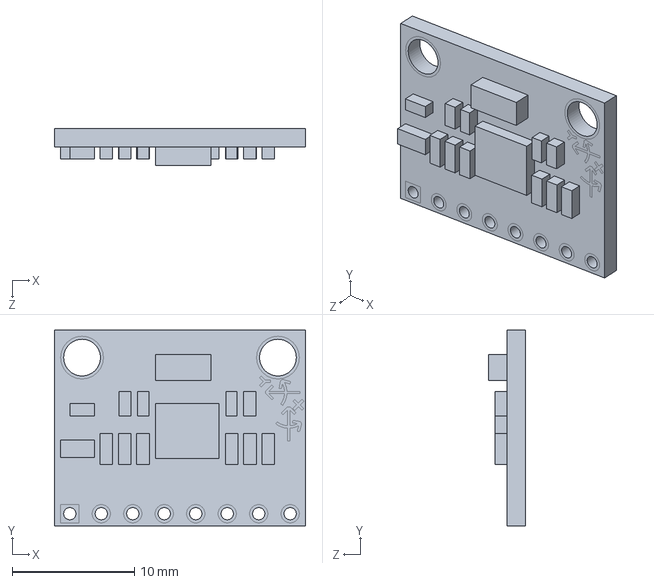
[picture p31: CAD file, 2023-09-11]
OneDrive_1_9-11-2023/Wiring Diagram/00A/MPU_6050.SLDASM
20.5 x 16.0 x 3.00 mm

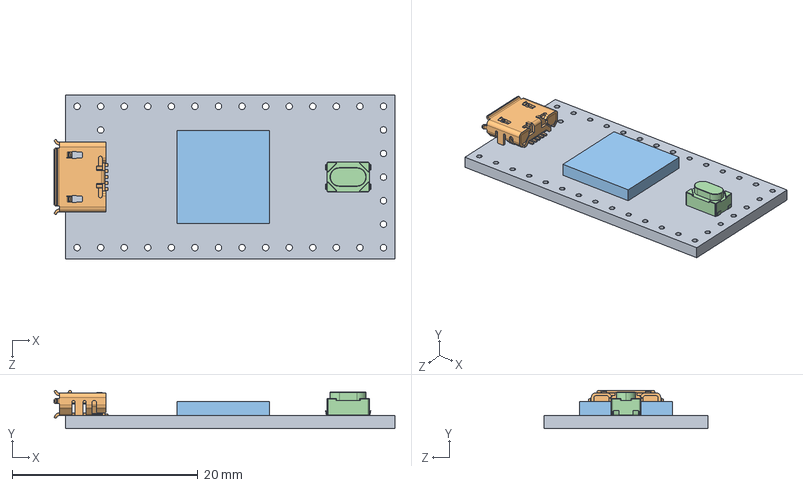
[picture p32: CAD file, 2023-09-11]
OneDrive_1_9-11-2023/Wiring Diagram/00A/Teensy_4.0_Assembly.SLDASM
36.8 x 4.12 x 17.7 mm
Teensy_4.0_PCB.STEP
Micro USB-B Female 5Pin SMD.STEP
NXP iMXRT1062.STEP
SKRPACE010 v4.STEP

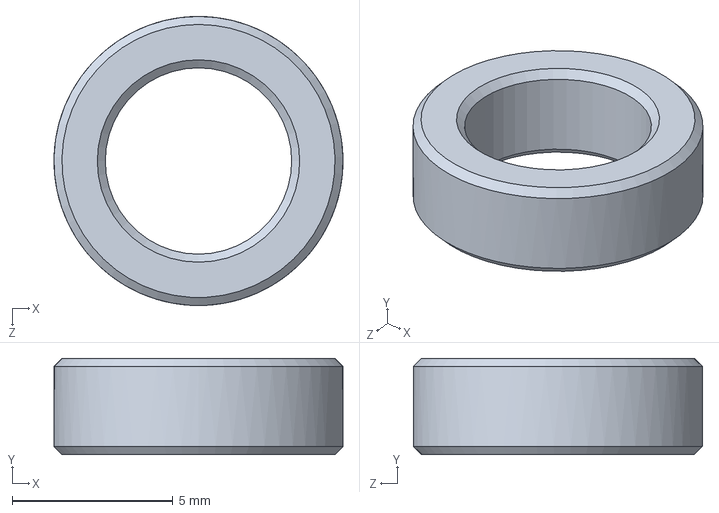
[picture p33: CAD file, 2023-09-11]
OneDrive_1_9-11-2023/Airfoil/Airfoil Hole Jig/Wing Spacer.SLDPRT
9.00 x 3.00 x 9.00 mm

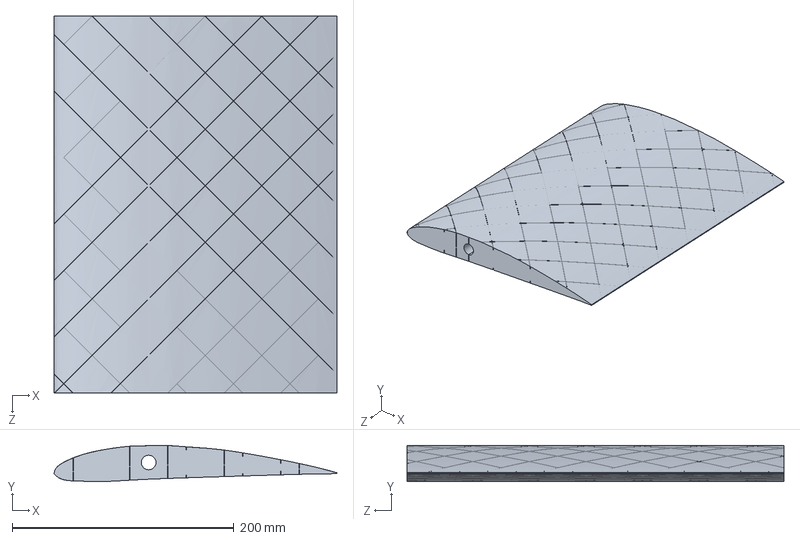
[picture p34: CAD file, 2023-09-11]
OneDrive_1_9-11-2023/Airfoil/v00A/NACA4412 Airfoil Left 00A.step.SLDPRT
255.0 x 32.5 x 340.0 mm

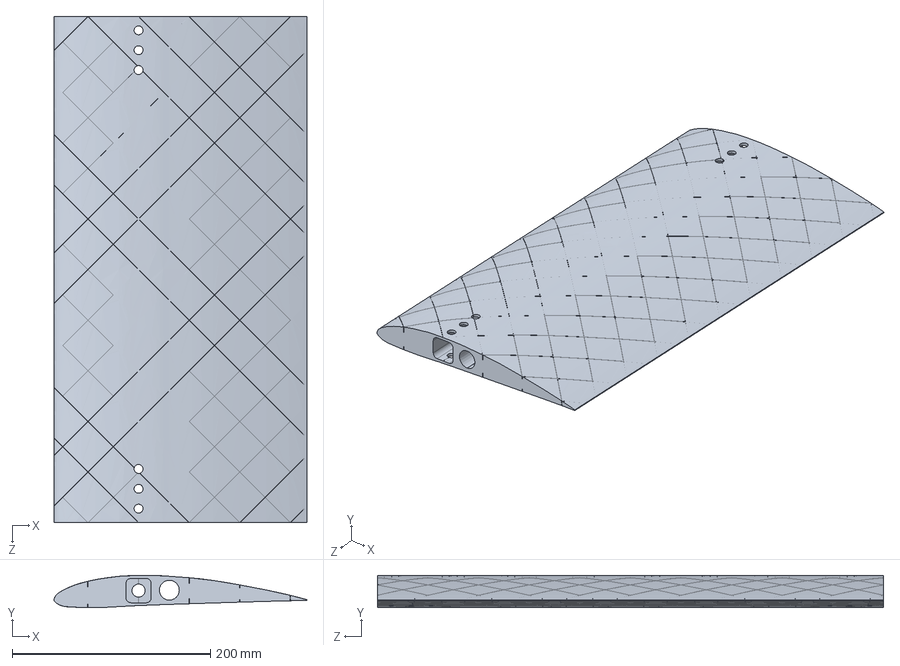
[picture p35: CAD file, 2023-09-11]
OneDrive_1_9-11-2023/Airfoil/v00B/NACA4412 Airfoil v00B.step.SLDPRT
255.0 x 32.5 x 510.0 mm

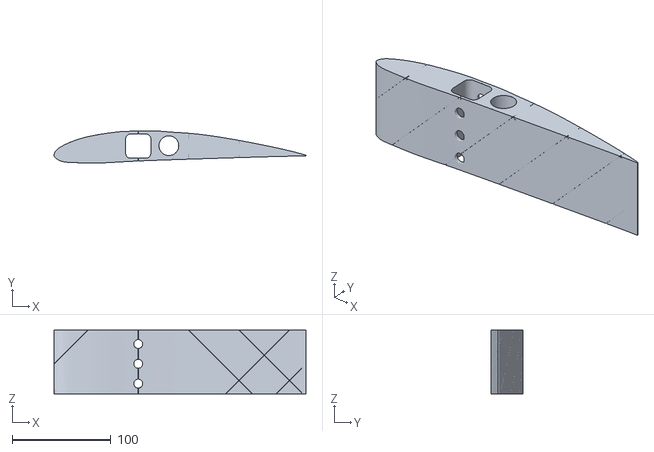
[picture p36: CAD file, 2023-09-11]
OneDrive_1_9-11-2023/Airfoil/v00C/NACA4412 Airfoil Part C v00C.stl
255.0 x 32.5 x 64.3

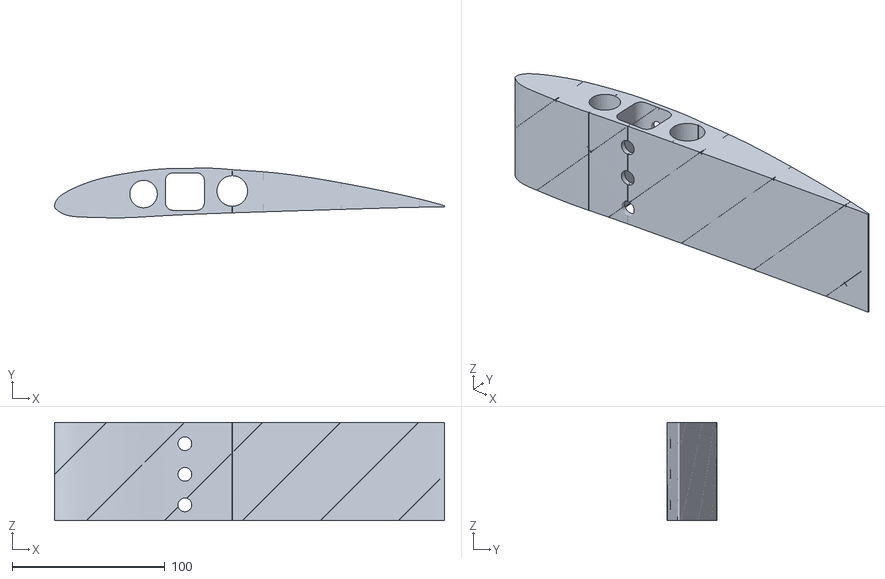
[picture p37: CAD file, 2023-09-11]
OneDrive_1_9-11-2023/Airfoil/v00D/NACA4412 Airfoil Part C v00D.stl
255.0 x 32.5 x 64.3

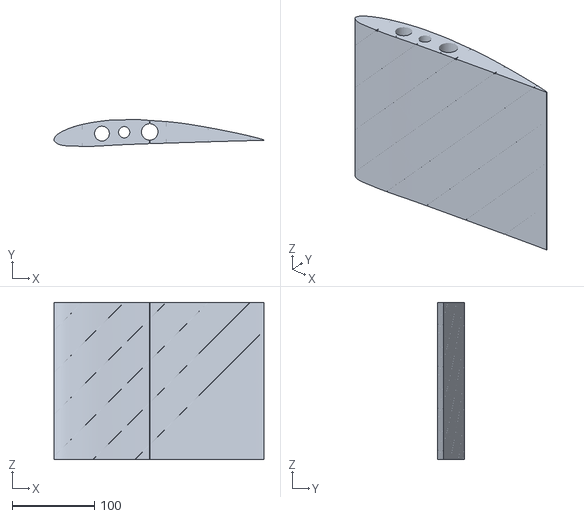
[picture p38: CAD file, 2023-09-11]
OneDrive_1_9-11-2023/Airfoil/v00E/NACA4412 Airfoil Half Right v00E.stl
255.0 x 32.5 x 190.7

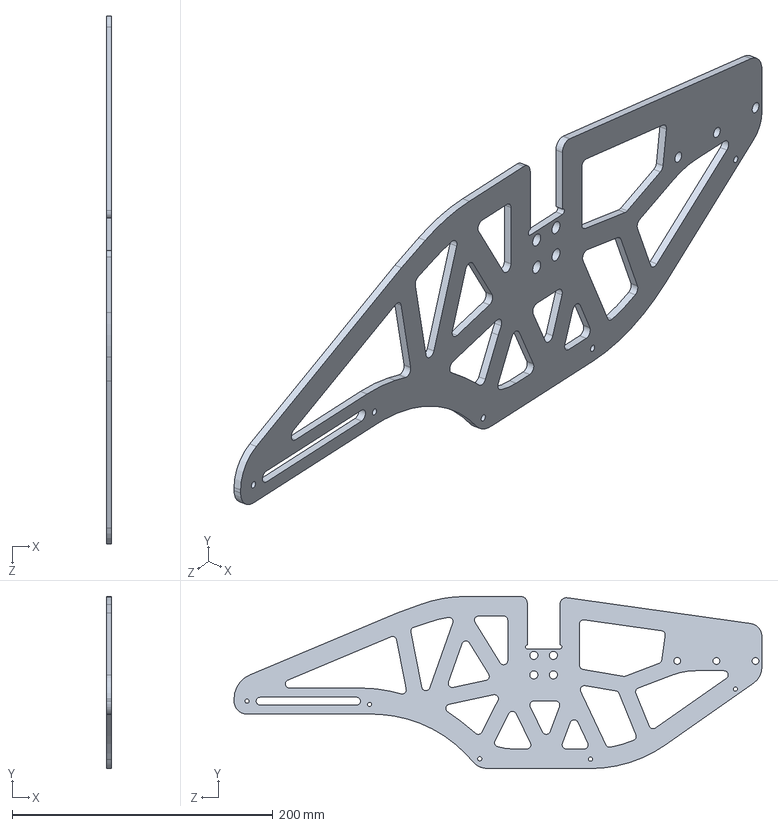
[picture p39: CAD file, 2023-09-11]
OneDrive_1_9-11-2023/Body/Side panels v1.SLDPRT
4.00 x 132.0 x 405.0 mm

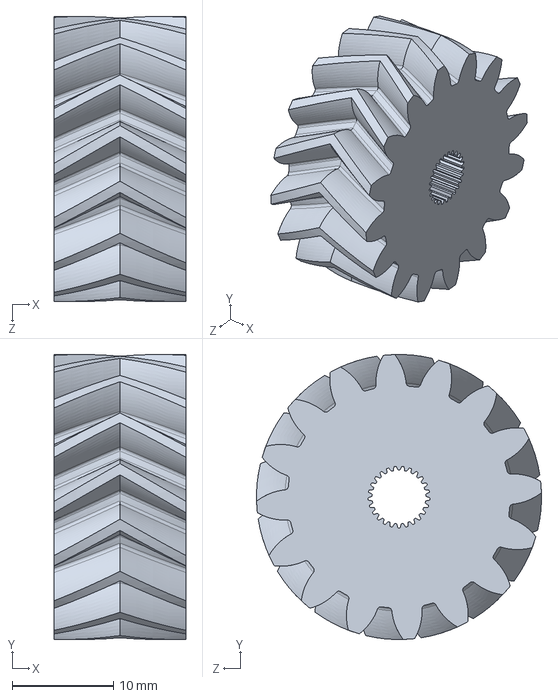
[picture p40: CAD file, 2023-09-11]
OneDrive_1_9-11-2023/Gears/Pinion.SLDPRT
13.0 x 28.1 x 28.1 mm

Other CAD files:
OneDrive_1_9-11-2023/Hardware/Rods/Carbon fiber rods.SLDPRT
OneDrive_1_9-11-2023/Mounts/Battery/battery_mount.SLDPRT
OneDrive_1_9-11-2023/Mounts/Landing Gear/Bottom Mount/v00A/Bottom Mount.SLDPRT
OneDrive_1_9-11-2023/Mounts/Landing Gear/Clamp/v00A/Clamp.SLDPRT
OneDrive_1_9-11-2023/Airfoil/Airfoil Hole Jig/Airfoil Hole Jig.SLDPRT
OneDrive_1_9-11-2023/Airfoil/Airfoil Hole Jig/Airfoil Hole Jig.STL
OneDrive_1_9-11-2023/Airfoil/Airfoil Hole Jig/Wing Spacer.STL
OneDrive_1_9-11-2023/Airfoil/v00A/Airfoil End Stabilizer v00A.SLDPRT
OneDrive_1_9-11-2023/Airfoil/v00A/Fusion 360 Files/NACA4412 Airfoil Left 00A.f3d
OneDrive_1_9-11-2023/Airfoil/v00A/Fusion 360 Files/NACA4412 Airfoil Right 00A.f3d
OneDrive_1_9-11-2023/Airfoil/v00A/NACA4412 Airfoil Ends 00A.step.SLDPRT
OneDrive_1_9-11-2023/Airfoil/v00A/NACA4412 Airfoil Right Wing 00A.step.SLDPRT
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

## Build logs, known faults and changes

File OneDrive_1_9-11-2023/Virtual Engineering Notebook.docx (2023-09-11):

ENGINEERING NOTEBOOK

Peter Cetner

ASSIGNED TO:

NAME: Piotr(Peter) Cetner

SIGNATURE: DATE: 1/26/2023

PHONE: (585)348-1924

EMAIL: onadeem@student.monroecc.edu OR onadeem157@gmail.com

COMPANY: Monroe Community College

DEPARTMENT: Engineering Science and Physics

ADDRESS: 1000 E. Henrietta Road

CITY: Rochester STATE: NY ZIP: 14623

TEAM MEMBERS:

Piotr(Peter) Cetner: pcetner@student.monroecc.edu

Omar Nadeem: onadeem@student.monroecc.edu

Maxim Karasev: mkarasev@student.monroecc.edu

TABLE OF CONTENTS

PAGE | SUBJECT | DATE
1-3 | Project Summary | 2/5/2023
4-5 | Grading Criteria, Weekly Goals, and Roles | 1/30/2023
6 | General Meeting #2 and Wingtip Design | 2/5/2023

While this Engineering Notebook is for a class, this project was started before the semester started. The purpose of this section is to detail the work done in those few weeks. I joined the project about two weeks after Maxim and Omar started, so some of the diagrams in this section are not my own.

Project Summary

An introduction to VTOL:
A VTOL vehicle, which stands for Vertical Take-off and Landing, is a vehicle that has the ability to take off vertically, and transition to a forward flight mode. This has numerous benefits when compared to traditional vertical takeoff vehicles and planes.

A VTOL is very similar to a helicopter/multirotor in that they also have the ability to take off vertically. However, that is where the similarities end. After takeoff, helicopters and other multirotors remain in the same configuration. Essentially, they rely on propellors to create lift by generating a force of thrust downwards. Because of this, the only way they are able to move in a direction other than up and down is by some sort of thrust vectoring. This is inherently very inefficient, as most of the force of thrust is used to keep the vehicle up, and only a small component of the force is used for movement.

In order to improve upon this, a VTOL has the ability to transition to a forward flight mode. Essentially, it transitions into a plane, with the propellors providing a thrust force opposite the intended direction of motion. Unlike a helicopter or multirotor, the main source of lift is an airfoil. This greatly improves efficiency and top speed.

While there are numerous types of VTOL aircraft, the design chosen by our team was one with a wing-tipped motor configuration. We plan on using two motors for propulsion, and two servo motors. By using a servo motor to tilt each of the propellors in the pitch direction by ~ +/- 20°, we expect to be able to have full control of the vehicle while hovering. Then, to allow for the transition between forward flight, we will have an additional servo motor or two to allow for an ~ 90° transition in the pitch direction. This transition will not only rotate the propellors, but also the whole wing.

Although all of the parts in the assembly shown below have already been designed, their design will not be discussed unless a change is required in the future.

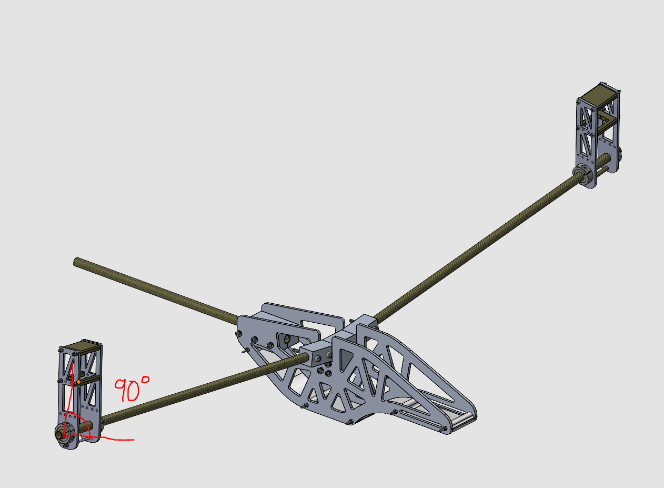
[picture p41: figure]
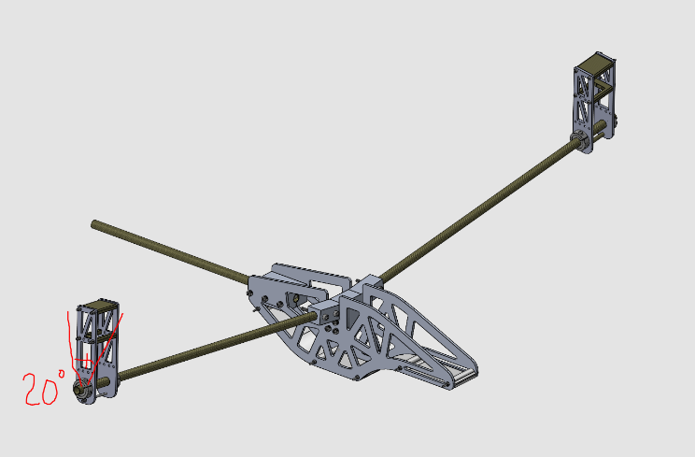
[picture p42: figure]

CONTINUED ON NEXT PAGE →

Motion Control:

Project Summary(Continued)

Maxim created this diagram of how we plan to control the VTOL:

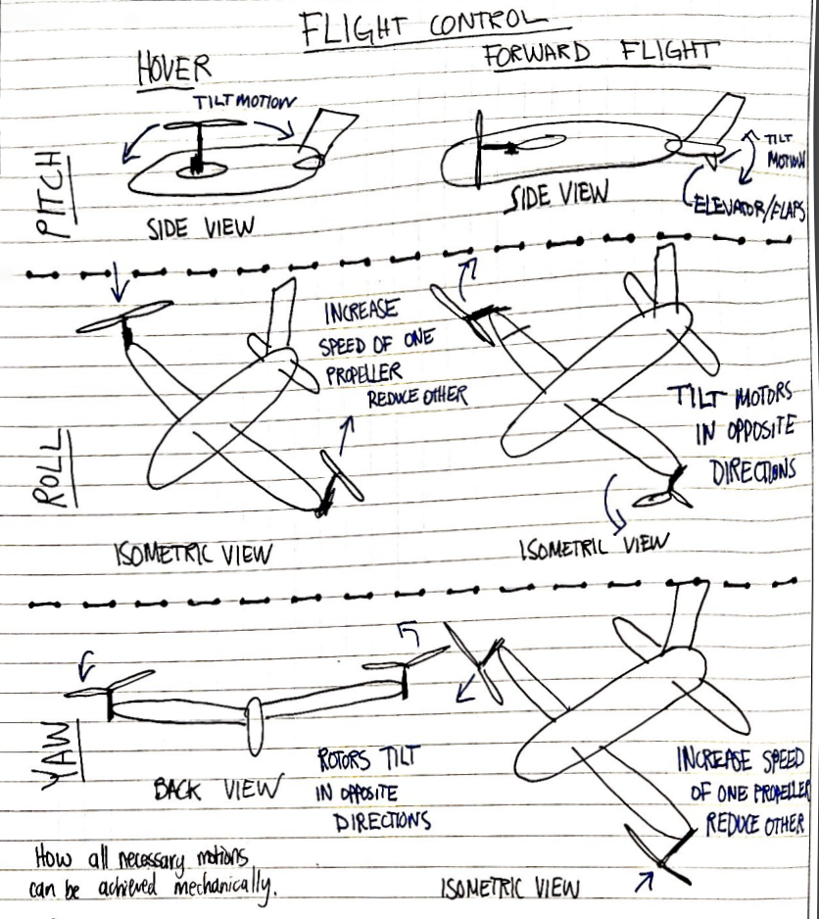
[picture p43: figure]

CONTINUED ON NEXT PAGE →

Flight controller:
Due to VTOL vehicles being relatively new, most consumer and hobbyist flight controllers are not compatible with VTOL vehicles. Because of this, we had to find a flight controller that would support our project, and we ended up finding the dRehmFlight flight controller, an experimental flight controller with specific compatibility for VTOL vehicles. It relies on a Teensy 4.0 microcontroller and MPU6050 6DOF IMU. We chose dRehmFlight because it has an incredible amount of clear and organized documentation. We have a flashed the controller, but have not done any coding other than that.

Project Summary(Continued)

Motor Tilt Mechanism:

Maxim created this diagram of how we plan to tilt each motor ~20°.

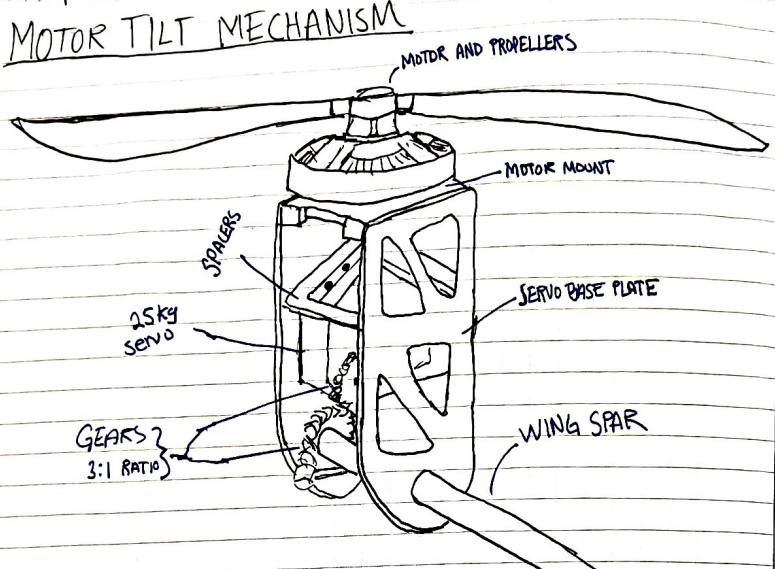
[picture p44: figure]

2/5/2023

January 29th, 2023, 7:30PM – 11:30PM

Grading Criteria, Weekly Goals, and Roles

Virtual meeting on Discord

Attending: Peter Cetner, Omar Nadeem, Maxim Karasev

Old business: Not applicable, this is the first meeting.

New business:

1. Due to our unique circumstance with this project, we had to come up with grading criteria for our independent project, such that it is equivalent to how a student in ENR 259 would be graded.

“Note: All other independent project groups will have different testing distribution based on the nature of the project. To conduct an independent project, you must receive an approval from your professor.” - ENR 259 Course Information Sheet

A student is usually graded under the following criteria:

1. (40%) Weekly Progress Review Meetings, Time Sheets and Engineering Notebooks

2. (10%) Testing 1: MCC-UAV A UAV must be capable of hovering one meter above the ground following the rules. The completion will be measured from 0% to 100%.

3. (10%) Testing 2: MCC-UAV A UGV must be capable of closely following the navigation line at all times to reach the target. The completion will be measured from 0% to 100%.

4. (10%) MCC Qualifier Competition: MCC-UAV A UGV must be capable of transporting an UAV through a series of ground navigation obstacles and release the UAV autonomously at the release zone. A UAV must be capable of navigation the line, disconnect maneuvering through the gates and be able to discharge the payloads following the rules.

5. (10%) ENR259 Course-Wide Competition: Your grade will be determined using the formula: Grade = (Your Team’s Score/The Highest Team’s Score)*100. If your team is conducting an independent project (must approved by your professor) testing guideline will establish accordingly.

6. (20%) Final Written and Oral/Poster Design Reporting

CONTINUED ON NEXT PAGE →

Our proposed grading to Professor Kumar:

Grading Criteria, Weekly Goals, and Roles (Continued)

1. (40%) Weekly Progress Review Meetings, Time Sheets and Engineering Notebooks

2. (10%) Testing 1: A vertical hover test, hovering one meter for 10 seconds. The flight mechanics of a VTOL are much more complicated when compared to a quadcopter, and as such, we would like to push this date forward by two weeks, to the week of March 13th.

3. (10%) Testing 2: A forward flight test, requiring the VTOL to take off vertically, then transition to forward flight. Due to potential tuning issues, we would like to push this date forward by two weeks as well, to the week of April 10th.

4. (20%) Full Flight Demonstration: As there is no competition for us to compete with our classmates, we would like to do a full flight demonstration. It is difficult to predict how agile our VTOL will be, so we would appreciate the guidance of Professor Kumar in how we proceed with this. We had two ideas for this, though they are a little rough.

a. Flight demonstration around the football field. By confining ourselves to a rather small area, we can demonstrate the ability of a VTOL to take off and land on the logo in the center of the field, as well as make sharp 90 degree turns while flying around the field.

b. Flight demonstration around the campus or a park. Theoretically, a VTOL is more efficient than a quadcopter. We propose flying a VTOL and a quadcopter for 5-10 minutes(TBD) and comparing the power consumption of each.

5. (20%) Final Written and Oral/Poster Design Reporting

As an addition to whatever is required for the poster and written report, we will also be presenting our project at Monroe Community College’s Scholars’ Day, given its unique nature.

2. We set ourselves the following goals for the coming week:

Omar: Finish CAD assembly
Maxim: Make/finalize the bill of materials (BOM)

Peter: Order parts and figure out how we can purchase materials ourselves with club funds.

3. Team roles were determined as follows:

Maxim: Project Manager
Peter: Mechanical Systems Manager

Omar: Electrical and Computer Systems Manager

Most of the duties of the Equipment and Materials Manager role do not apply to us due to us being an independent project, so the remaining responsibilities of that role will be split between the three of us.

Uunfortunately, the first week of classes has required that we dedicate a large amount of time to administrative work for the Engineering Leadership Council as well as the UAV team. As those issues get sorted, we should have more time for actually working on our project.

1/31/2023

Febuary 4th, 2023, 7:30PM – 11:30PM

General Meeting #2 and Wingtip Design

Attending: Peter Cetner, Omar Nadeem, Maxim Karasev

Old business:

Progress report:

Omar: Finish updating CAD assembly → Completed.

Maxim: Make/finalize the bill of materials (BOM) → BOM has all current parts

Peter: Order parts and figure out how we can purchase materials ourselves with club funds. → Completed.

Unfortunately, the ordering of materials using our club funds is more complicated than it should be, so I won’t detail the process here. I chose the hardware we will be using from McMaster-Carr and forwarded it to the required person for it to be purchased.

New business:

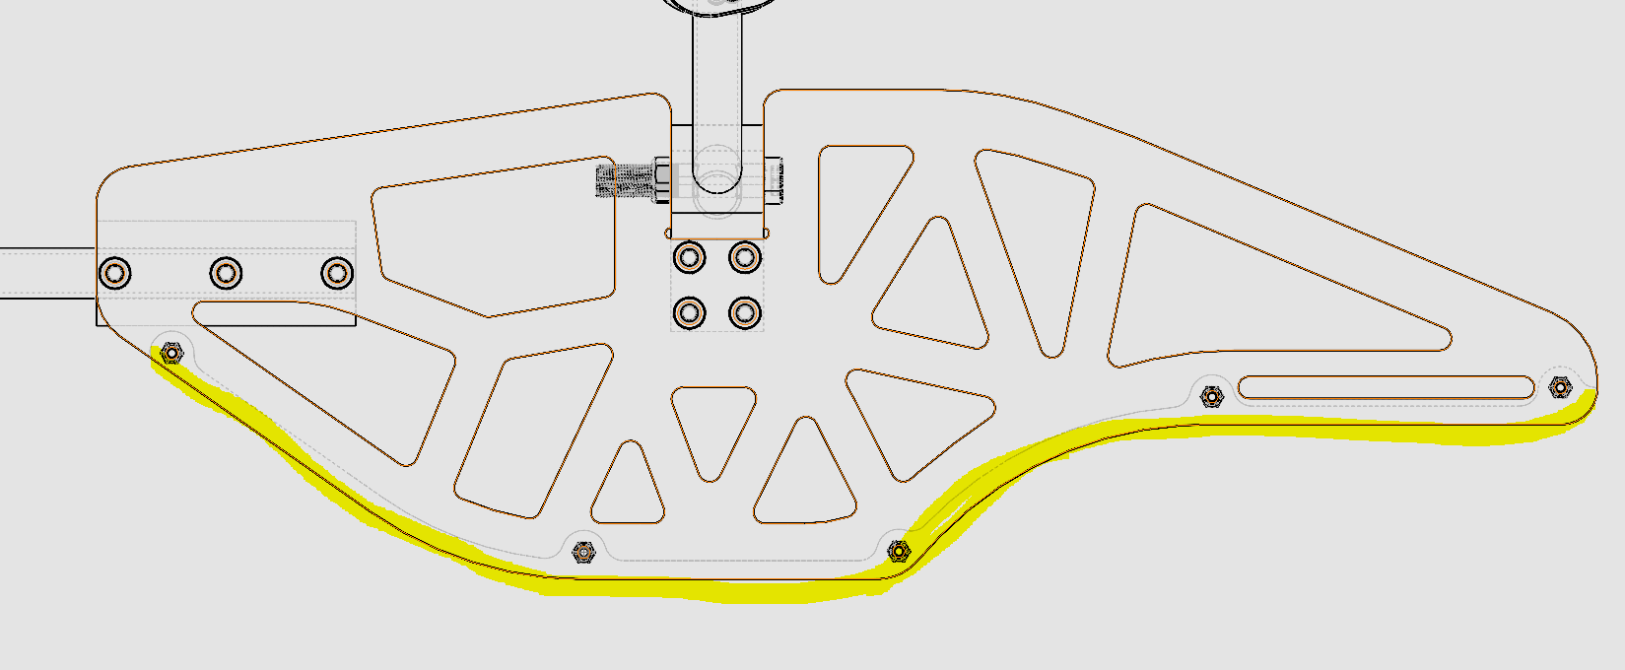
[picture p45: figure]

During our meeting we discussed numerous topics, such as what we accomplished from the previous meeting. I discussed how I fixed the bottom plate contour so that it perfectly matches the side panel, as it being slightly off was driving me crazy.

Besides talking about what Omar and Maxim did, we spent most of the meeting trying to determine our next steps for the project. While discussing the plans for the motor tilt mechanism, I managed to catch a very small mistake that would have really set us back. The servo motor we planned to use had a 180° range of motion, and Omar planned to use a 1:3 gearing ratio. Unfortunately for us, 180°/3 = 60°, not 90°. This would have cause major problems had we waited until the servo motors arrived, but since we caught it early, we are able to order new servo motors with a 270° range of motion, as well as reduce the gearing slightly, giving us more than 100° range of motion.

CONTINUED ON NEXT PAGE →

The rest of the meeting was spent discussing how we would create our wings and tail airfoils. We decided that 3d printing was the best method of manufacturing, as it is relatively cheap and quick. A long-term solution could be custom carbon fiber molded wings, as they would be very durable and light weight, but it would be extremely expensive. 3d printed wings, while not the most lightweight or durable, are extremely easy to remake if we break them. Just print the STL file again, and in a few hours, you will have a brand new wing, with no work on your part. This is something extremely unique to 3d printing, no other manufacturing technology allows you to do something like that. Based off of some research, we picked a NACA 4412 airfoil for both the tail and the wings. None of us have any experience running fluid dynamics simulations, so we chose to rely on what others have used for VTOL vehicles. In the end, we decided that even if we pick a “bad” airfoil, then all we have to do is redesign the wing and reprint it; The time cost of trying to figure out the absolute “best” airfoil just isn’t worth it for our prototype vehicle.

General Meeting #2 and Wingtip Design (Continued)

We set ourselves the following goals for the coming week:

Omar: Finalize the motor tilt mechanism and machine/3d print any necessary to roughly prototype the design.

Maxim: Design the VTOL’s wings.

Peter: Send email to Joel Eisele about machining parts and design the VTOL’s tail.

For my work following the meeting I made a sub-assembly for the wing tipped motor servo mounts. The sub assembly includes a total of a front and back panel, multiple spacers, a servo and a motor. The spacers are to create support and mounting locations for both the motor and servo. The panels include a shaft hole that is the size of the carbon fiber rods 13.1mm in which this assembly and the airfoils will be fixed to. The wiring will be cleanly tucked away within the carbon fiber rods down to the fuselage where they will hook up to the necessary electronics. There is still more work to be done such as the gearing to the servo, and new shaft collars in which we can print and fasten them to the carbon fiber rods. The gearing will be done with a 2.5:1 or a 2:1 ratio. This will provide us with more than enough torque while not losing out on angle of rotation for the transition to and from forward flight.

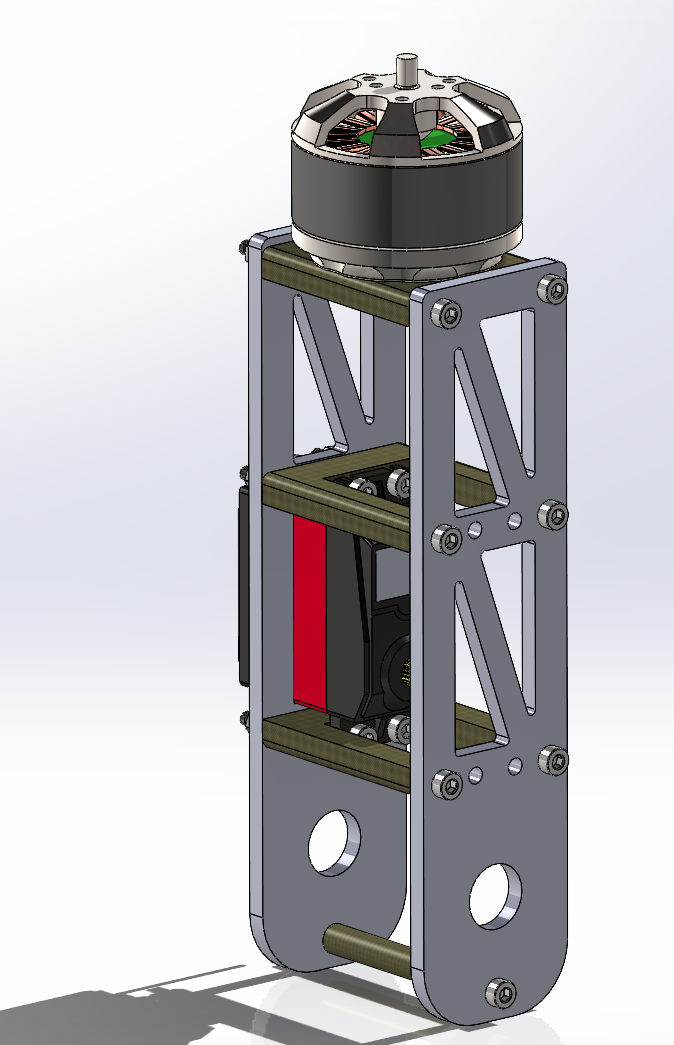
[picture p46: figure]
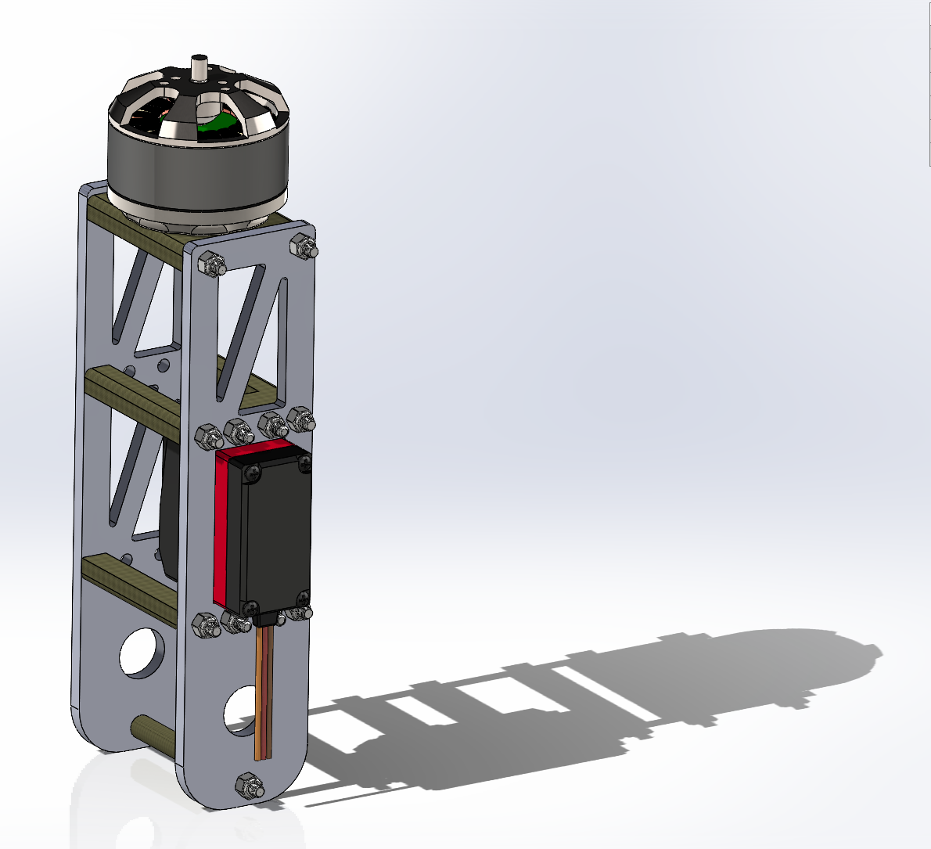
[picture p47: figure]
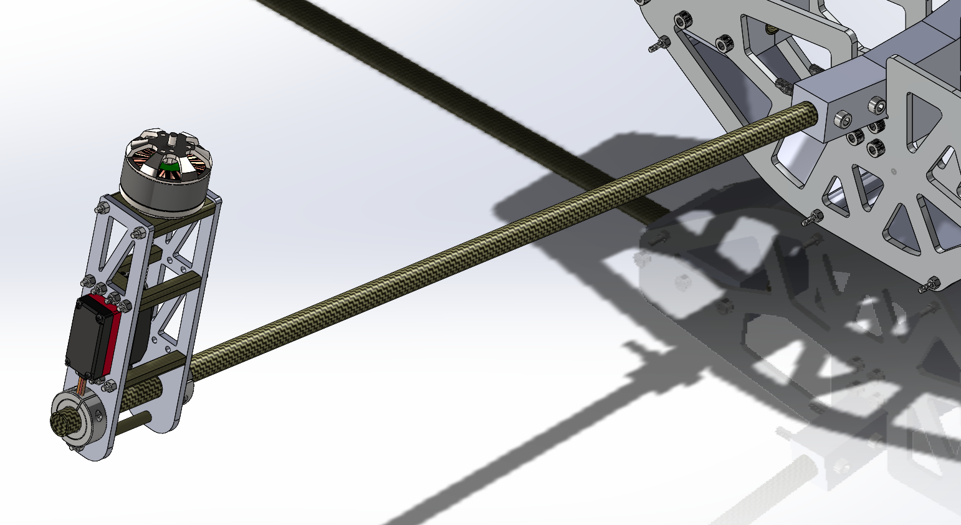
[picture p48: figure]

2/6/2023

SIGNATURE DATE PROPRIETARY INFORMATION

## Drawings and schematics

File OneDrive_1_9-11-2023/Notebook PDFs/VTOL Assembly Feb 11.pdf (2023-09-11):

## VTOL ASSEMBLY

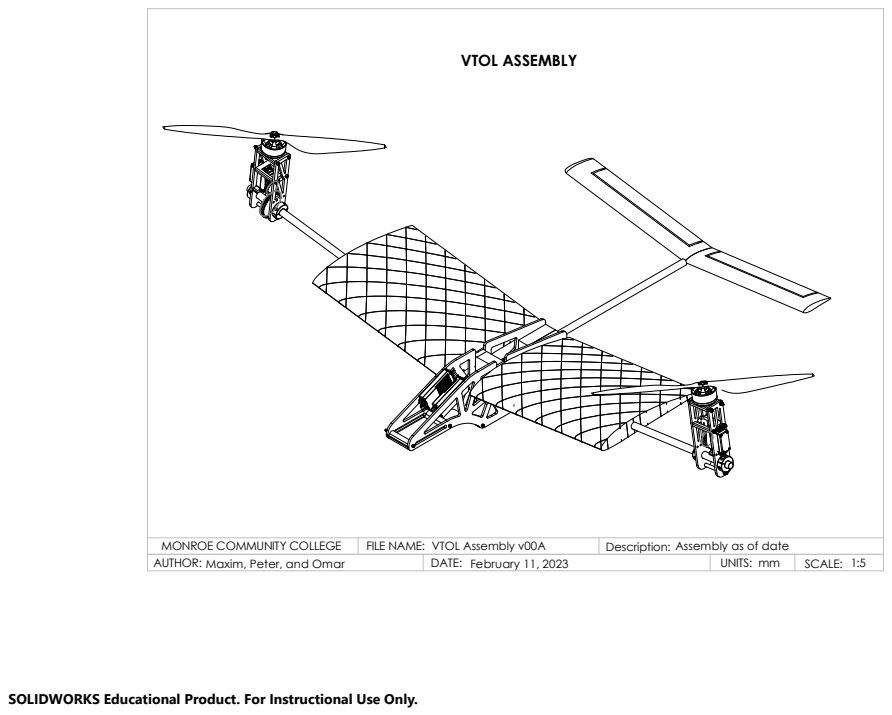
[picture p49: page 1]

MONROE COMMUNITY COLLEGE | FILE NAME: VTOL Assembly v00A | Description: Assembly as of date
AUTHOR: Maxim, Peter, and Omar | DATE: February 11, 2023 | UNITS: mm | SCALE: 1:5

SOLIDWORKS Educational Product. For Instructional Use Only.

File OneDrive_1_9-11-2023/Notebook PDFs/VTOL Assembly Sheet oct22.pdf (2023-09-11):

## VTOL ASSEMBLY

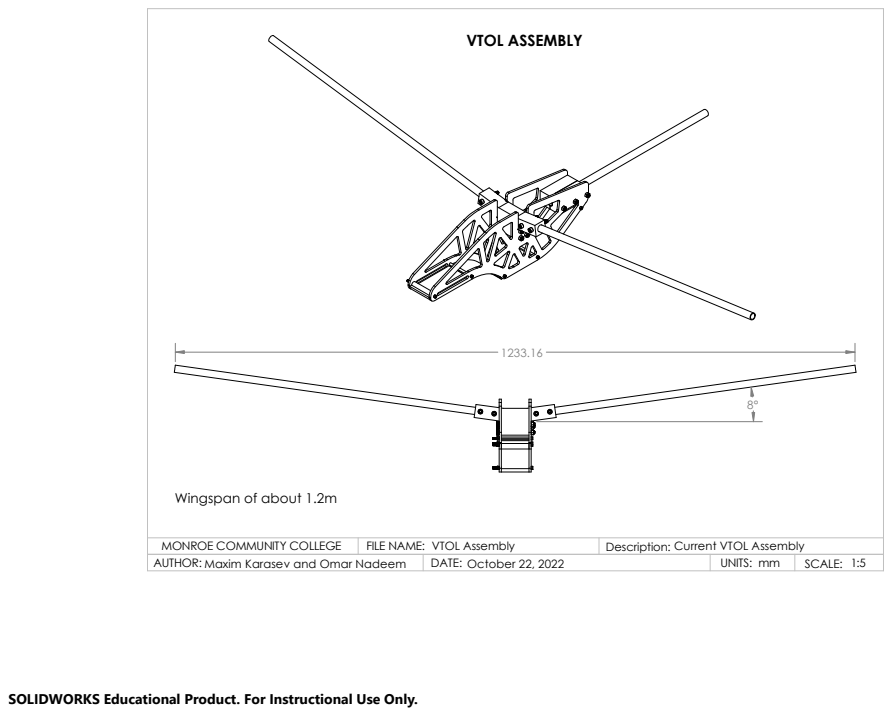
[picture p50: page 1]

Wingspan of about 1.2m

MONROE COMMUNITY COLLEGE | FILE NAME: VTOL Assembly | Description: Current VTOL Assembly
AUTHOR: Maxim Karasev and Omar Nadeem | DATE: October 22, 2022 | UNITS: mm | SCALE: 1:5

SOLIDWORKS Educational Product. For Instructional Use Only.

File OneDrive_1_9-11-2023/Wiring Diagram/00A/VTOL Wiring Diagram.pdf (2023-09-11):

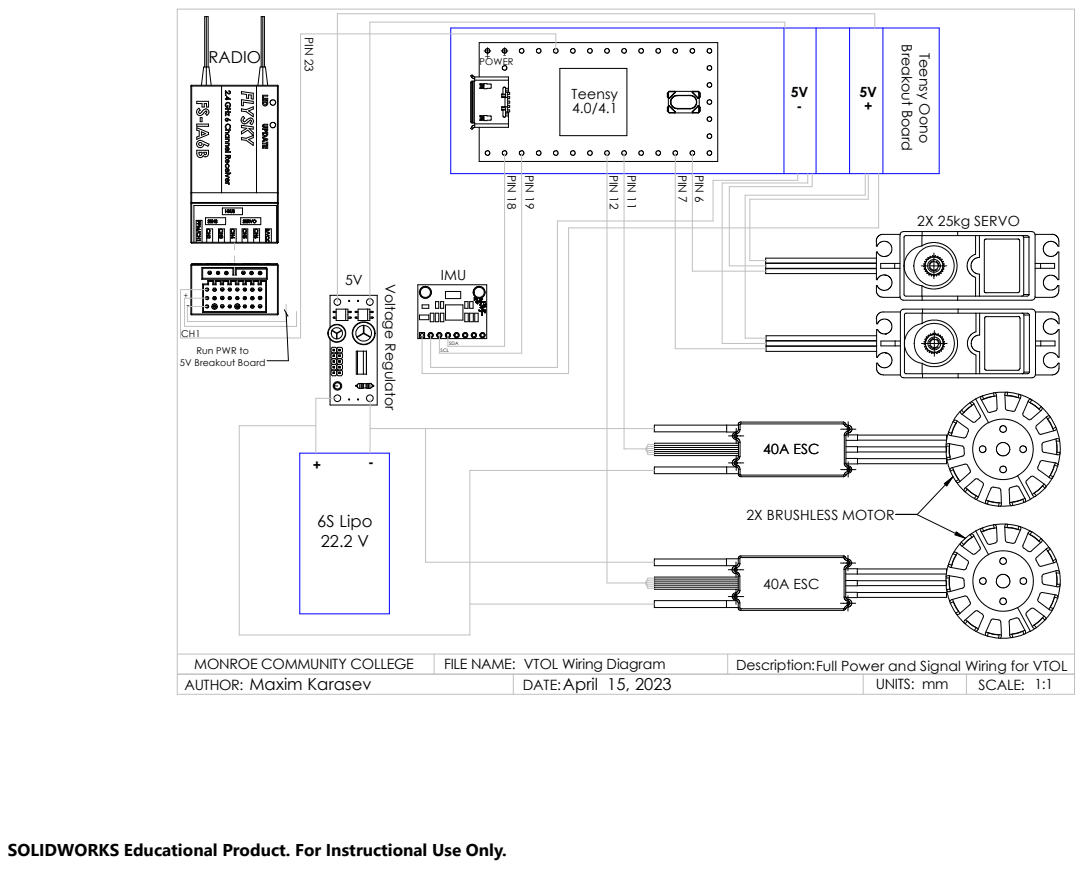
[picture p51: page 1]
2X 25kg SERVO; Te ensy O; ono; Bre akout Bo; ard; 40A ESC; 2X BRUSHLESS MOTOR PIN 18 PIN 19; PIN 12 PIN 11; PIN 7 PIN 6 PIN 23; SCL; SDA; IMU; olta; gulator; POWER-; 6S Lipo; Teensy; RADIO

Run PWR to
5V Breakout Board

MONROE COMMUNITY COLLEGE | FILE NAME: VTOL Wiring Diagram | Description: Full Power and Signal Wiring for VTOL
Maxim Karasev AUTHOR: | April 15, 2023 DATE: | UNITS: mm | SCALE: 1:1

SOLIDWORKS Educational Product. For Instructional Use Only.

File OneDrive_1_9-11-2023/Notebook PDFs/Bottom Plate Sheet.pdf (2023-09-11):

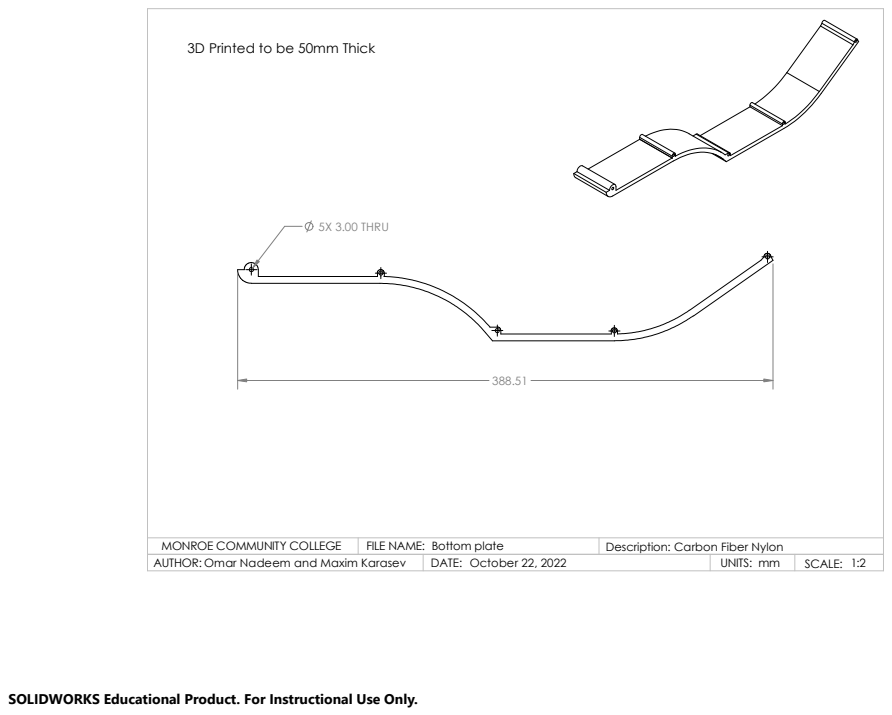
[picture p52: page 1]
5X 3.00 THRU

3D Printed to be 50mm Thick

MONROE COMMUNITY COLLEGE | FILE NAME: Bottom plate | Description: Carbon Fiber Nylon
AUTHOR: Omar Nadeem and Maxim Karasev | DATE: October 22, 2022 | UNITS: mm | SCALE: 1:2

SOLIDWORKS Educational Product. For Instructional Use Only.

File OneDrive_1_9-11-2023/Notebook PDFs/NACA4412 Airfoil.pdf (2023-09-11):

## NACA 4412 AIRFOIL

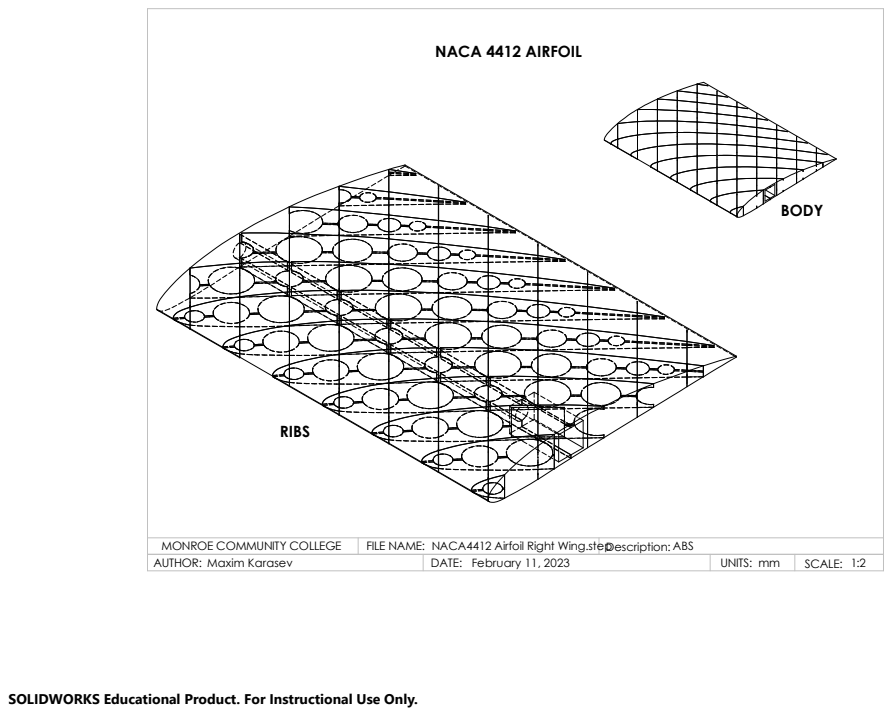
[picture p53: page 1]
BODY; RIBS

MONROE COMMUNITY COLLEGE | FILE NAME: NACA4412 Airfoil Right Wing.stepDescription: | ABS
AUTHOR: Maxim Karasev | DATE: February 11, 2023 | UNITS: mm | SCALE: 1:2

SOLIDWORKS Educational Product. For Instructional Use Only.

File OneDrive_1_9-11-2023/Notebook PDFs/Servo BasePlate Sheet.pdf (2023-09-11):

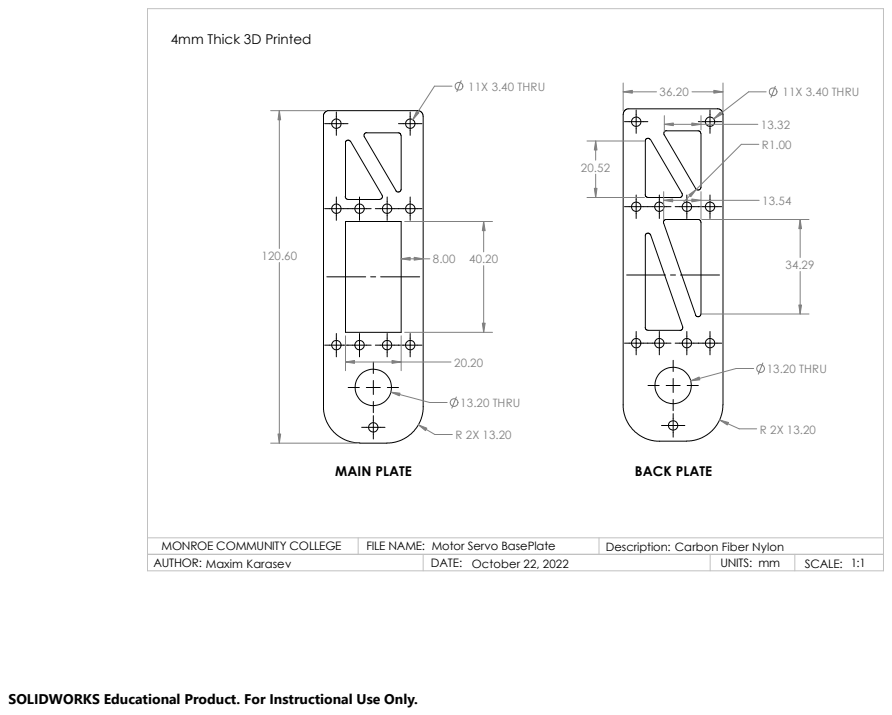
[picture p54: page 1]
4mm Thick 3D Printed; MAIN PLATE; BACK PLATE; 13.20 THRU; 11X 3.40 THRU

MONROE COMMUNITY COLLEGE | FILE NAME: Motor Servo BasePlate | Description: Carbon Fiber Nylon
AUTHOR: Maxim Karasev | DATE: October 22, 2022 | UNITS: mm | SCALE: 1:1

SOLIDWORKS Educational Product. For Instructional Use Only.

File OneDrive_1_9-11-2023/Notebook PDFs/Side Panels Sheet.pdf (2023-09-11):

4

3

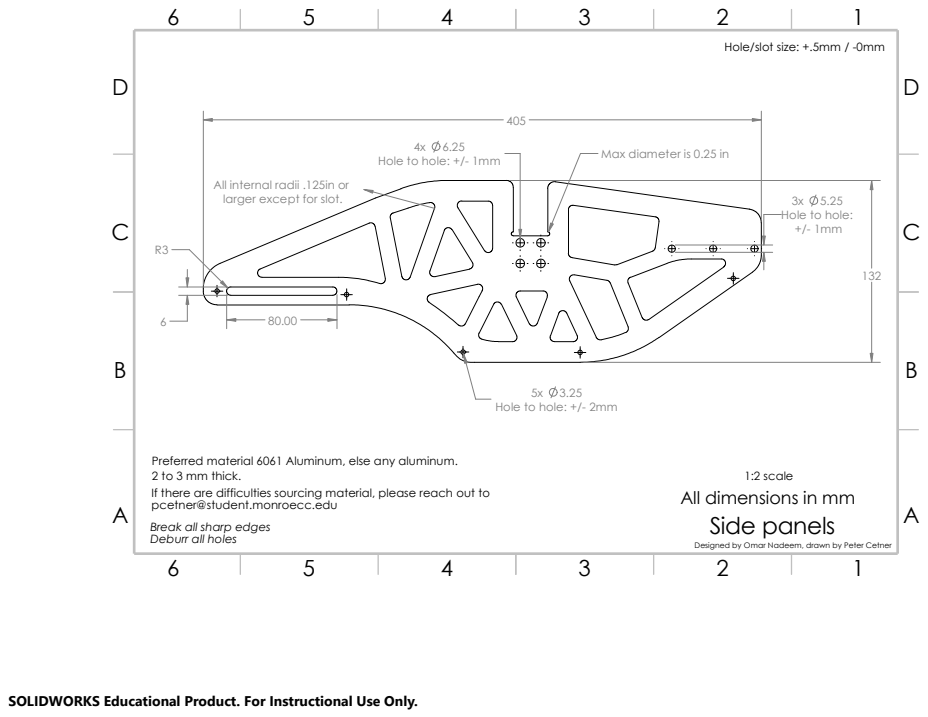
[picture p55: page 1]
Side panels; If there are difficulties sourcing material, please reach out to; All dimensions in mm; 2 to 3 mm thick.; 1:2 scale

Hole/slot size: +.5mm / -0mm

Hole to hole: +/- 1mm

Max diameter is 0.25 in

All internal radii .125in or
larger except for slot.

Hole to hole:

Hole to hole: +/- 2mm

Preferred material 6061 Aluminum, else any aluminum.
pcetner@student.monroecc.edu
Break all sharp edges
Deburr all holes

Designed by Omar Nadeem, drawn by Peter Cetner

SOLIDWORKS Educational Product. For Instructional Use Only.

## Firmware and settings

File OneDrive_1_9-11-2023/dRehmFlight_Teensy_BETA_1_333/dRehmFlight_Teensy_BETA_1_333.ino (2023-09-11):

//Arduino/Teensy Flight Controller - dRehmFlight
//Author: Nicholas Rehm
//Project Start: 1/6/2020
//Last Updated: 7/29/2022
//Version: Beta 1.3
 
//========================================================================================================================//

//CREDITS + SPECIAL THANKS
/*
Some elements inspired by:
http://www.brokking.net/ymfc-32_main.html

Madgwick filter function adapted from:
https://github.com/arduino-libraries/MadgwickAHRS

MPU9250 implementation based on MPU9250 library by:
brian.taylor@bolderflight.com
http://www.bolderflight.com

Thank you to:
RcGroups 'jihlein' - IMU implementation overhaul + SBUS implementation.
Everyone that sends me pictures and videos of your flying creations! -Nick

*/



//========================================================================================================================//
//                                                 USER-SPECIFIED DEFINES                                                 //                                                                 
//========================================================================================================================//

//Uncomment only one receiver type
//#define USE_PWM_RX
#define USE_PPM_RX
//#define USE_SBUS_RX
//#define USE_DSM_RX
static const uint8_t num_DSM_channels = 6; //If using DSM RX, change this to match the number of transmitter channels you have

//Uncomment only one IMU
#define USE_MPU6050_I2C //Default
//#define USE_MPU9250_SPI

//Uncomment only one full scale gyro range (deg/sec)
#define GYRO_250DPS //Default
//#define GYRO_500DPS
//#define GYRO_1000DPS
//#define GYRO_2000DPS

//Uncomment only one full scale accelerometer range (G's)
#define ACCEL_2G //Default
//#define ACCEL_4G
//#define ACCEL_8G
//#define ACCEL_16G



//========================================================================================================================//



//REQUIRED LIBRARIES (included with download in main sketch folder)

#include <Wire.h>     //I2c communication
#include <SPI.h>      //SPI communication
#include <PWMServo.h> //Commanding any extra actuators, installed with teensyduino installer

#if defined USE_SBUS_RX
  #include "src/SBUS/SBUS.h"   //sBus interface
#endif

#if defined USE_DSM_RX
  #include "src/DSMRX/DSMRX.h"  
#endif

#if defined USE_MPU6050_I2C
  #include "src/MPU6050/MPU6050.h"
  MPU6050 mpu6050;
#elif defined USE_MPU9250_SPI
  #include "src/MPU9250/MPU9250.h"
  MPU9250 mpu9250(SPI2,36);
#else
  #error No MPU defined... 
#endif



//========================================================================================================================//



//Setup gyro and accel full scale value selection and scale factor

#if defined USE_MPU6050_I2C
  #define GYRO_FS_SEL_250    MPU6050_GYRO_FS_250
  #define GYRO_FS_SEL_500    MPU6050_GYRO_FS_500
  #define GYRO_FS_SEL_1000   MPU6050_GYRO_FS_1000
  #define GYRO_FS_SEL_2000   MPU6050_GYRO_FS_2000
  #define ACCEL_FS_SEL_2     MPU6050_ACCEL_FS_2
  #define ACCEL_FS_SEL_4     MPU6050_ACCEL_FS_4
  #define ACCEL_FS_SEL_8     MPU6050_ACCEL_FS_8
  #define ACCEL_FS_SEL_16    MPU6050_ACCEL_FS_16
#elif defined USE_MPU9250_SPI
  #define GYRO_FS_SEL_250    mpu9250.GYRO_RANGE_250DPS
  #define GYRO_FS_SEL_500    mpu9250.GYRO_RANGE_500DPS
  #define GYRO_FS_SEL_1000   mpu9250.GYRO_RANGE_1000DPS                                                        
  #define GYRO_FS_SEL_2000   mpu9250.GYRO_RANGE_2000DPS
  #define ACCEL_FS_SEL_2     mpu9250.ACCEL_RANGE_2G
  #define ACCEL_FS_SEL_4     mpu9250.ACCEL_RANGE_4G
  #define ACCEL_FS_SEL_8     mpu9250.ACCEL_RANGE_8G
  #define ACCEL_FS_SEL_16    mpu9250.ACCEL_RANGE_16G
#endif
  
#if defined GYRO_250DPS
  #define GYRO_SCALE GYRO_FS_SEL_250
  #define GYRO_SCALE_FACTOR 131.0
#elif defined GYRO_500DPS
  #define GYRO_SCALE GYRO_FS_SEL_500
  #define GYRO_SCALE_FACTOR 65.5
#elif defined GYRO_1000DPS
  #define GYRO_SCALE GYRO_FS_SEL_1000
  #define GYRO_SCALE_FACTOR 32.8
#elif defined GYRO_2000DPS
  #define GYRO_SCALE GYRO_FS_SEL_2000
  #define GYRO_SCALE_FACTOR 16.4
#endif

#if defined ACCEL_2G
  #define ACCEL_SCALE ACCEL_FS_SEL_2
  #define ACCEL_SCALE_FACTOR 16384.0
#elif defined ACCEL_4G
  #define ACCEL_SCALE ACCEL_FS_SEL_4
  #define ACCEL_SCALE_FACTOR 8192.0
#elif defined ACCEL_8G
  #define ACCEL_SCALE ACCEL_FS_SEL_8
  #define ACCEL_SCALE_FACTOR 4096.0
#elif defined ACCEL_16G
  #define ACCEL_SCALE ACCEL_FS_SEL_16
  #define ACCEL_SCALE_FACTOR 2048.0
#endif



//========================================================================================================================//
//                                               USER-SPECIFIED VARIABLES                                                 //                           
//========================================================================================================================//

//Radio failsafe values for every channel in the event that bad reciever data is detected. Recommended defaults:
unsigned long channel_1_fs = 1000; //thro
unsigned long channel_2_fs = 1500; //ail
unsigned long channel_3_fs = 1500; //elev
unsigned long channel_4_fs = 1500; //rudd
unsigned long channel_5_fs = 2000; //gear, greater than 1500 = throttle cut
unsigned long channel_6_fs = 2000; //aux1

//Filter parameters - Defaults tuned for 2kHz loop rate; Do not touch unless you know what you are doing:
float B_madgwick = 0.04;  //Madgwick filter parameter
float B_accel = 0.14;     //Accelerometer LP filter paramter, (MPU6050 default: 0.14. MPU9250 default: 0.2)
float B_gyro = 0.1;       //Gyro LP filter paramter, (MPU6050 default: 0.1. MPU9250 default: 0.17)
float B_mag = 1.0;        //Magnetometer LP filter parameter

//Magnetometer calibration parameters - if using MPU9250, uncomment calibrateMagnetometer() in void setup() to get these values, else just ignore these
float MagErrorX = 0.0;
float MagErrorY = 0.0; 
float MagErrorZ = 0.0;
float MagScaleX = 1.0;
float MagScaleY = 1.0;
float MagScaleZ = 1.0;

//IMU calibration parameters - calibrate IMU using calculate_IMU_error() in the void setup() to get these values, then comment out calculate_IMU_error()
float AccErrorX = 0.0;
float AccErrorY = 0.0;
float AccErrorZ = 0.0;
float GyroErrorX = 0.0;
float GyroErrorY= 0.0;
float GyroErrorZ = 0.0;

//Controller parameters (take note of defaults before modifying!): 
float i_limit = 25.0;     //Integrator saturation level, mostly for safety (default 25.0)
float maxRoll = 40;     //Max roll angle in degrees for angle mode (maximum ~70 degrees), deg/sec for rate mode 
float maxPitch = 25;    //Max pitch angle in degrees for angle mode (maximum ~70 degrees), deg/sec for rate mode
float maxYaw = 40;     //Max yaw rate in deg/sec 160

float Kp_roll_angle = 0.5;    //Roll P-gain - angle mode 
float Ki_roll_angle = 0.3;    //Roll I-gain - angle mode
float Kd_roll_angle = 0.15;   //Roll D-gain - angle mode (has no effect on controlANGLE2)
float B_loop_roll = 0.9;      //Roll damping term for controlANGLE2(), lower is more damping (must be between 0 to 1)

float Kp_pitch_angle = .25;   //Pitch P-gain - angle mode 0.2
float Ki_pitch_angle = .3;   //Pitch I-gain - angle mode 0.3
float Kd_pitch_angle = .08;  //Pitch D-gain - angle mode (has no effect on controlANGLE2) 0.05
float B_loop_pitch = 0.9;     //Pitch damping term for controlANGLE2(), lower is more damping (must be between 0 to 1)

float Kp_yaw = 0.2;          //Yaw P-gain 0.3
float Ki_yaw = .03;           //Yaw I-gain 0.05 (.01)
float Kd_yaw = 0.0001;       //Yaw D-gain (be careful when increasing too high, motors will begin to overheat!) 0.00015


//BELOW ARE PIDs that DO NOT APPPLY, as they are rate (Acro) mode

float Kp_pitch_rate = 0.0;   //Pitch P-gain - rate mode 0.15
float Ki_pitch_rate = 0.0;    //Pitch I-gain - rate mode 0.2
float Kd_pitch_rate = 0.0; //Pitch D-gain - rate mode (be careful when increasing too high, motors will begin to overheat!) 0.0002

float Kp_roll_rate = 0.15;    //Roll P-gain - rate mode
float Ki_roll_rate = 0.2;     //Roll I-gain - rate mode
float Kd_roll_rate = 0.0002;  //Roll D-gain - rate mode (be careful when increasing too high, motors will begin to overheat!)

//========================================================================================================================//
//                                                     DECLARE PINS                                                       //                           
//========================================================================================================================//                                          

//NOTE: Pin 13 is reserved for onboard LED, pins 18 and 19 are reserved for the MPU6050 IMU for default setup
//Radio:
//Note: If using SBUS, connect to pin 21 (RX5), if using DSM, connect to pin 15 (RX3)
const int ch1Pin = 15; //throttle
const int ch2Pin = 16; //ail
const int ch3Pin = 17; //ele
const int ch4Pin = 20; //rudd
const int ch5Pin = 21; //gear (throttle cut)
const int ch6Pin = 22; //aux1 (free aux channel)
const int PPM_Pin = 23;
//OneShot125 ESC pin outputs:
const int m1Pin = 0;
const int m2Pin = 1;
const int m3Pin = 2;
const int m4Pin = 3;
const int m5Pin = 4;
const int m6Pin = 5;
//PWM servo or ESC outputs:
const int servo1Pin = 6;
const int servo2Pin = 7;
const int servo3Pin = 8;
const int servo4Pin = 9;
const int servo5Pin = 10;
const int servo6Pin = 11;
const int servo7Pin = 12;
PWMServo servo1;  //Create servo objects to control a servo or ESC with PWM
PWMServo servo2;
PWMServo servo3;
PWMServo servo4;
PWMServo servo5;
PWMServo servo6;
PWMServo servo7;



//========================================================================================================================//



//DECLARE GLOBAL VARIABLES

//General stuff
float dt;
unsigned long current_time, prev_time;
unsigned long print_counter, serial_counter;
unsigned long blink_counter, blink_delay;
bool blinkAlternate;

//Radio communication:
unsigned long channel_1_pwm, channel_2_pwm, channel_3_pwm, channel_4_pwm, channel_5_pwm, channel_6_pwm;
unsigned long channel_1_pwm_prev, channel_2_pwm_prev, channel_3_pwm_prev, channel_4_pwm_prev;

#if defined USE_SBUS_RX
  SBUS sbus(Serial5);
  uint16_t sbusChannels[16];
  bool sbusFailSafe;
  bool sbusLostFrame;
#endif
#if defined USE_DSM_RX
  DSM1024 DSM;
#endif

//IMU:
float AccX, AccY, AccZ;
float AccX_prev, AccY_prev, AccZ_prev;
float GyroX, GyroY, GyroZ;
float GyroX_prev, GyroY_prev, GyroZ_prev;
float MagX, MagY, MagZ;
float MagX_prev, MagY_prev, MagZ_prev;
float roll_IMU, pitch_IMU, yaw_IMU;
float roll_IMU_prev, pitch_IMU_prev;
float q0 = 1.0f; //Initialize quaternion for madgwick filter
float q1 = 0.0f;
float q2 = 0.0f;
float q3 = 0.0f;

//Normalized desired state:
float thro_des, roll_des, pitch_des, yaw_des;
float roll_passthru, pitch_passthru, yaw_passthru;

//Controller:
float error_roll, error_roll_prev, roll_des_prev, integral_roll, integral_roll_il, integral_roll_ol, integral_roll_prev, integral_roll_prev_il, integral_roll_prev_ol, derivative_roll, roll_PID = 0;
float error_pitch, error_pitch_prev, pitch_des_prev, integral_pitch, integral_pitch_il, integral_pitch_ol, integral_pitch_prev, integral_pitch_prev_il, integral_pitch_prev_ol, derivative_pitch, pitch_PID = 0;
float error_yaw, error_yaw_prev, integral_yaw, integral_yaw_prev, derivative_yaw, yaw_PID = 0;

//Mixer
float m1_command_scaled, m2_command_scaled, m3_command_scaled, m4_command_scaled, m5_command_scaled, m6_command_scaled;
int m1_command_PWM, m2_command_PWM, m3_command_PWM, m4_command_PWM, m5_command_PWM, m6_command_PWM;
float s1_command_scaled, s2_command_scaled, s3_command_scaled, s4_command_scaled, s5_command_scaled, s6_command_scaled, s7_command_scaled;
int s1_command_PWM, s2_command_PWM, s3_command_PWM, s4_command_PWM, s5_command_PWM, s6_command_PWM, s7_command_PWM;
float servo_vertical = .5;  


//========================================================================================================================//
//                                                      VOID SETUP                                                        //                           
//========================================================================================================================//
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
   *  Simulates the void loop(), but only for the purpose of providing throttle pass through to the motors, so that you can
   *  power up with throttle at full, let ESCs begin arming sequence, and lower throttle to zero. This function should only be
   *  uncommented when performing an ESC calibration.
   */
   while (true) {
      prev_time = current_time;      
      current_time = micros();      
      dt = (current_time - prev_time)/1000000.0;
    
      digitalWrite(13, HIGH); //LED on to indicate we are not in main loop

      getCommands(); //Pulls current available radio commands
      failSafe(); //Prevent failures in event of bad receiver connection, defaults to failsafe values assigned in setup
      getDesState(); //Convert raw commands to normalized values based on saturated control limits
      getIMUdata(); //Pulls raw gyro, accelerometer, and magnetometer data from IMU and LP filters to remove noise
      Madgwick(GyroX, -GyroY, -GyroZ, -AccX, AccY, AccZ, MagY, -MagX, MagZ, dt); //Updates roll_IMU, pitch_IMU, and yaw_IMU (degrees)
      getDesState(); //Convert raw commands to normalized values based on saturated control limits
      
      m1_command_scaled = thro_des;
      m2_command_scaled = thro_des;
      m3_command_scaled = thro_des;
      m4_command_scaled = thro_des;
      m5_command_scaled = thro_des;
      m6_command_scaled = thro_des;
      s1_command_scaled = thro_des;
      s2_command_scaled = thro_des;
      s3_command_scaled = thro_des;
      s4_command_scaled = thro_des;
      s5_command_scaled = thro_des;
      s6_command_scaled = thro_des;
      s7_command_scaled = thro_des;
      scaleCommands(); //Scales motor commands to 125 to 250 range (oneshot125 protocol) and servo PWM commands to 0 to 180 (for servo library)
    
      //throttleCut(); //Directly sets motor commands to low based on state of ch5
      
      servo1.write(s1_command_PWM); 
      servo2.write(s2_command_PWM);
      servo3.write(s3_command_PWM);
      servo4.write(s4_command_PWM);
      servo5.write(s5_command_PWM);
      servo6.write(s6_command_PWM);
      servo7.write(s7_command_PWM);
      commandMotors(); //Sends command pulses to each motor pin using OneShot125 protocol
      
      //printRadioData(); //Radio pwm values (expected: 1000 to 2000)
      
      loopRate(2000); //Do not exceed 2000Hz, all filter parameters tuned to 2000Hz by default
   }
}

float floatFaderLinear(float param, float param_min, float param_max, float fadeTime, int state, int loopFreq){
  //DESCRIPTION: Linearly fades a float type variable between min and max bounds based on desired high or low state and time
  /*  
   *  Takes in a float variable, desired minimum and maximum bounds, fade time, high or low desired state, and the loop frequency 
   *  and linearly interpolates that param variable between the maximum and minimum bounds. This function can be called in controlMixer()
   *  and high/low states can be determined by monitoring the state of an auxillarly radio channel. For example, if channel_6_pwm is being 
   *  monitored to switch between two dynamic configurations (hover and forward flight), this function can be called within the logical 
   *  statements in order to fade controller gains, for example between the two dynamic configurations. The 'state' (1 or 0) can be used
   *  to designate the two final options for that control gain based on the dynamic configuration assignment to the auxillary radio channel.
   *  
   */
  float diffParam = (param_max - param_min)/(fadeTime*loopFreq); //Difference to add or subtract from param for each loop iteration for desired fadeTime

  if (state == 1) { //Maximum param bound desired, increase param by diffParam for each loop iteration
    param = param + diffParam;
  }
  else if (state == 0) { //Minimum param bound desired, decrease param by diffParam for each loop iteration
    param = param - diffParam;
  }

  param = constrain(param, param_min, param_max); //Constrain param within max bounds
  
  return param;
}

float floatFaderLinear2(float param, float param_des, float param_lower, float param_upper, float fadeTime_up, float fadeTime_down, int loopFreq){
  //DESCRIPTION: Linearly fades a float type variable from its current value to the desired value, up or down
  /*  
   *  Takes in a float variable to be modified, desired new position, upper value, lower value, fade time, and the loop frequency 
   *  and linearly fades that param variable up or down to the desired value. This function can be called in controlMixer()
   *  to fade up or down between flight modes monitored by an auxillary radio channel. For example, if channel_6_pwm is being 
   *  monitored to switch between two dynamic configurations (hover and forward flight), this function can be called within the logical 
   *  statements in order to fade controller gains, for example between the two dynamic configurations. 
   *  
   */
  if (param > param_des) { //Need to fade down to get to desired
    float diffParam = (param_upper - param_des)/(fadeTime_down*loopFreq);
    param = param - diffParam;
  }
  else if (param < param_des) { //Need to fade up to get to desired
    float diffParam = (param_des - param_lower)/(fadeTime_up*loopFreq);
    param = param + diffParam;
  }

  param = constrain(param, param_lower, param_upper); //Constrain param within max bounds
  
  return param;
}

void switchRollYaw(int reverseRoll, int reverseYaw) {
  //DESCRIPTION: Switches roll_des and yaw_des variables for tailsitter-type configurations
  /*
   * Takes in two integers (either 1 or -1) corresponding to the desired reversing of the roll axis and yaw axis, respectively.
   * Reversing of the roll or yaw axis may be needed when switching between the two for some dynamic configurations. Inputs of 1, 1 does not 
   * reverse either of them, while -1, 1 will reverse the output corresponding to the new roll axis. 
   * This function may be replaced in the future by a function that switches the IMU data instead (so that angle can also be estimated with the 
   * IMU tilted 90 degrees from default level).
   */
  float switch_holder;

  switch_holder = yaw_des;
  yaw_des = reverseYaw*roll_des;
  roll_des = reverseRoll*switch_holder;
}

void throttleCut() {
  //DESCRIPTION: Directly set actuator outputs to minimum value if triggered
  /*
   * Monitors the state of radio command channel_5_pwm and directly sets the mx_command_PWM values to minimum (120 is
   * minimum for oneshot125 protocol, 0 is minimum for standard PWM servo library used) if channel 5 is high. This is the last function 
   * called before commandMotors() is called so that the last thing checked is if the user is giving permission to command
   * the motors to anything other than minimum value. Safety first. 
   */
  if (channel_5_pwm > 1500) {
    m1_command_PWM = 120;
    m2_command_PWM = 120;
    m3_command_PWM = 120;
    m4_command_PWM = 120;
    m5_command_PWM = 120;
    m6_command_PWM = 120;
    
    //Uncomment if using servo PWM variables to control motor ESCs
    //s1_command_PWM = 0;
    //s2_command_PWM = 0;
    //s3_command_PWM = 0;
    //s4_command_PWM = 0;
    //s5_command_PWM = 0;
    s6_command_PWM = 0;
    s7_command_PWM = 0;


    //PETER 4/19/2023 We are having issues with the failsafe throttlecut functionality, I have pinpointed the issue to the above lines. We are using servo PWM vars to control our BLDC motor ESCs, and the appropriate lines(s6 and s7) were commented out.
  }
}
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
